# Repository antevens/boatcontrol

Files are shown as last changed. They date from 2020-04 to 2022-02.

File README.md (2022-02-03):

# Prototype, use at your own risk

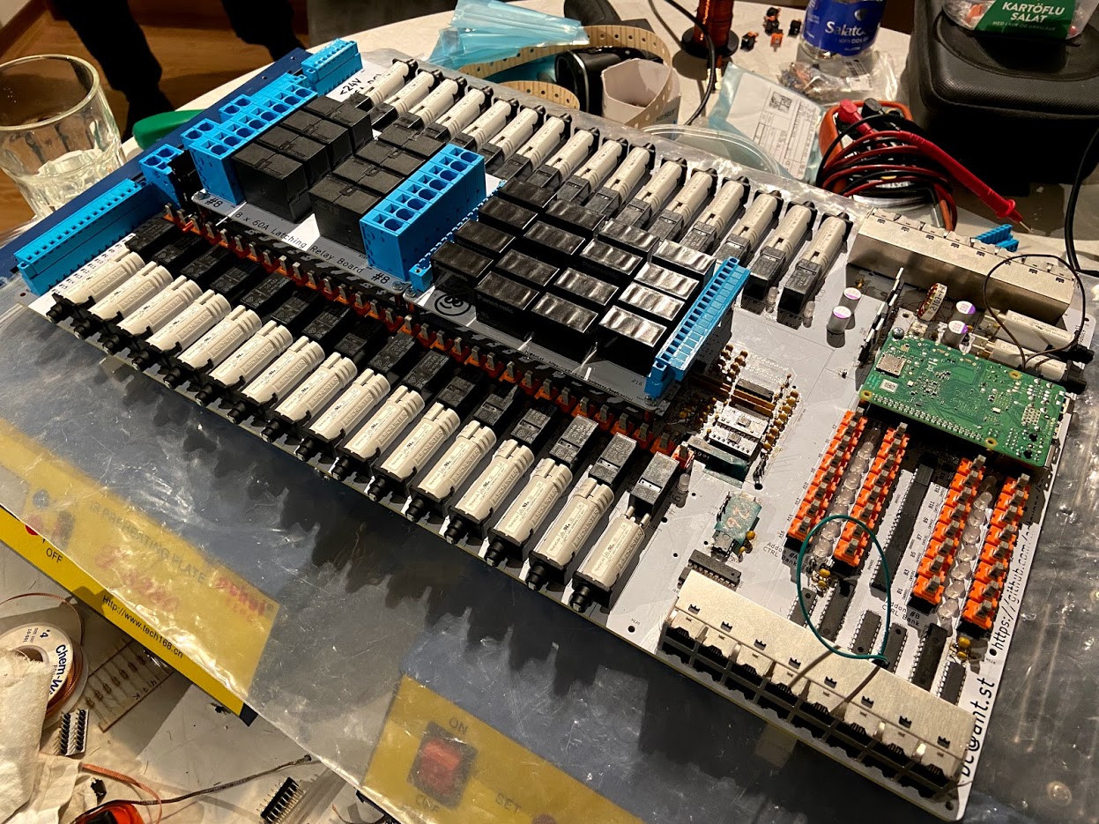
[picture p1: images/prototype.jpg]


# Boatcontrol

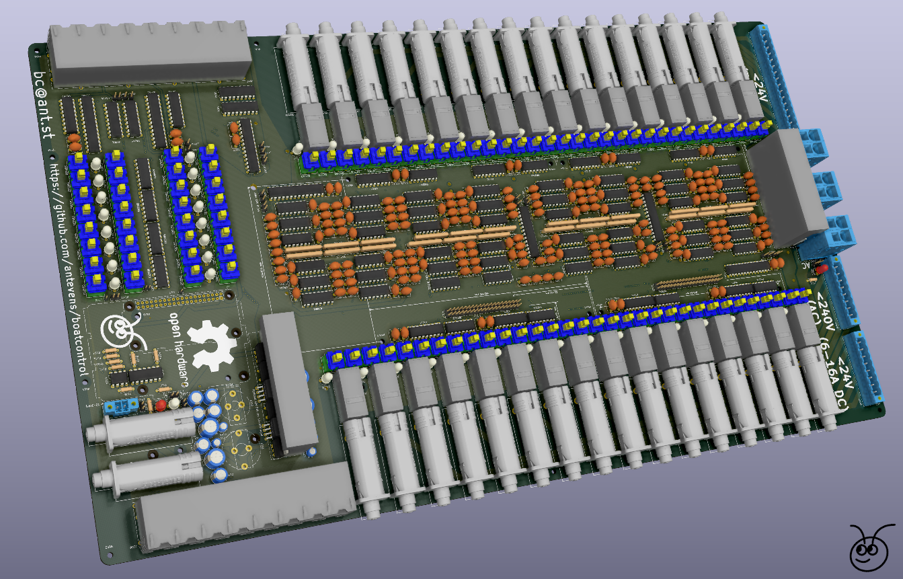
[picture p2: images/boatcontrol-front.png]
Boatcontrol Rendering_Front

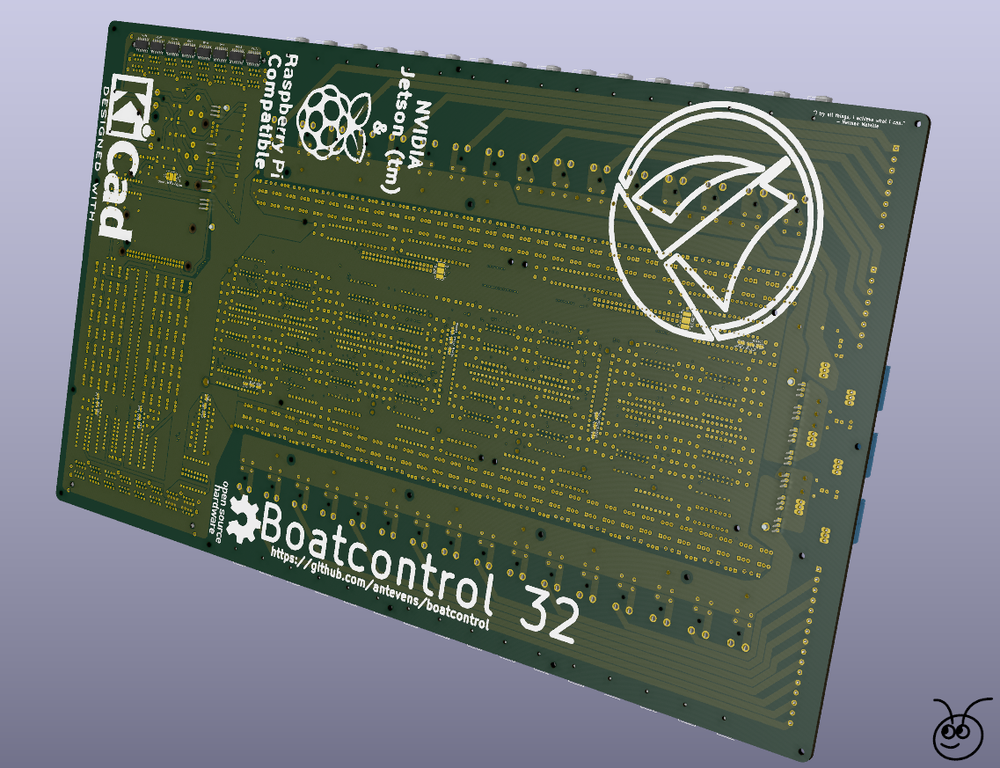
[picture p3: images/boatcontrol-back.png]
Boatcontrol Rendering_Front


## About

Boatcontrol is an open hardware design for a marine grade SMART/IoT electrical
distribution panel and electronics platform (boat) controller.

It's an I/O breakout board capable of switching 32 onboard laching relays and
optionally 32 momentary/laching relays using addon boards switchnig  up to 60A
AC/DC 0-400V per circuit.

The "smart" part is provided by either a **Raspberry Pi** HAT or a
**Nvidia Jetson** (Nano/Xavier NX) either of which can be mounted on the board.

All critical parts are designed to be field serviceable, components using
through-holes are used where possible for better durability in mobile marine
environment. Note that these boards need to carry significant amounts of current
and high voltage and as such PCB thickness and clearances are CRITICAL along
with proper thermal management.

Special care has been taken to limit idle power consumption wherever possible, on
it's own the board will only consume 15 Milliwatts when idle, if a Raspberry Pi (RPi) Zero is
mated it will add 80-120 Milliwatts, a fully fledged RPi 4 with all the bells and
whistles will add up to 3.4 Watts, a Jetson Xavier NX will bring the total to
10-15 Watts depending on configuration. Jumpers are provided where applicable
to disable LEDs to reduce power consumption when idle. Each active indicator LED
will likely consume 10-20 Milliwatts. Note that using a momentary add-on board can increase
the power consumption substancially depending on which relays are used and how
much time they spend on the "ON" position.

Effort was taken to make the boards as reliable as possible and enable them to
be operated in emergencies and under failure conditions. All circuits can be
operated manually on the board as long as the board has a power source over 6v
and below 30v (see optional 12V vs 24V operation and PSU).
Operation using external 5V TTL inputs via the RJ45 connectors is
available regardless of the state or presence of the RPi/Jetson.

The board can be set to run in either 12V or 24V mode, for operation
over 13V please make sure the optional 12V PSU components are in place and
the appropriate solder jumpers bridged.
For 12V operation make sure the 12V bypass jumper/solder pads are bridged.

## PCB Stack & Manufacturing

The design includes a main board and (at the time of launch) two optional addon
boards, the primary board is designed for 4 layer 2.4-3.2mm PCBs with the following sizes/layers:

#### Main board - 536mm x 308mm (just over 21" x 12")
* Front Power, 6oz (220um) copper, min spacing 0.500mm)
* First Signal, 1oz (35um) copper, min spacing 0.250mm)
* Second Signal, 1oz (35um) copper, min spacing 0.250mm)
* Back Power, 6oz (220um) copper, min spacing 0.500mm)

#### Addon boards - 153mm x 106mm (just over 5" x 4")
* The high current daughter board is designed for 4 layer 1/13oz (35/450um) copper.
* The non-latching daughter board is designed for 4 layer 1/6oz (35/200um) copper.
* The non-existent current sensing daughter board .. will probably use 6oz copper.
* The non-existent Full ESD optocoupler/isolator board .. will probably use 1oz copper.

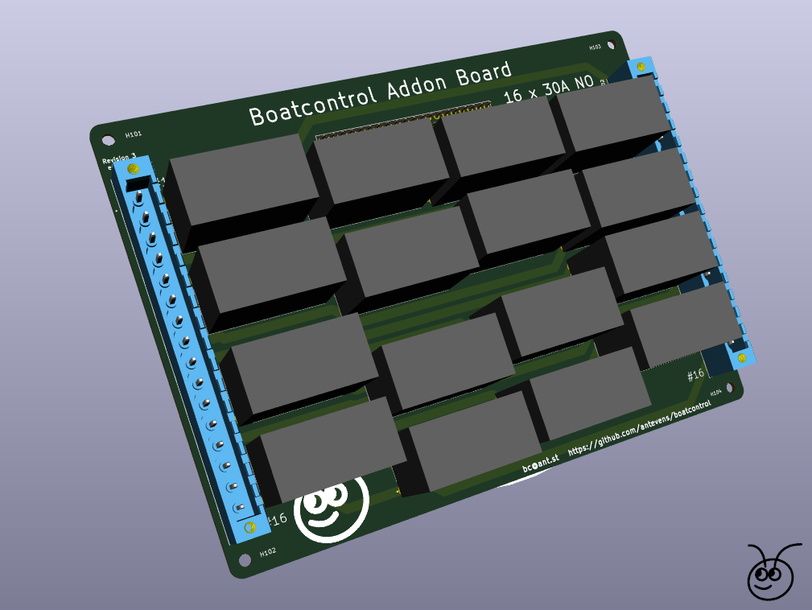
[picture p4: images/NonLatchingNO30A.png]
Boatcontrol Non Latching Relay Addon

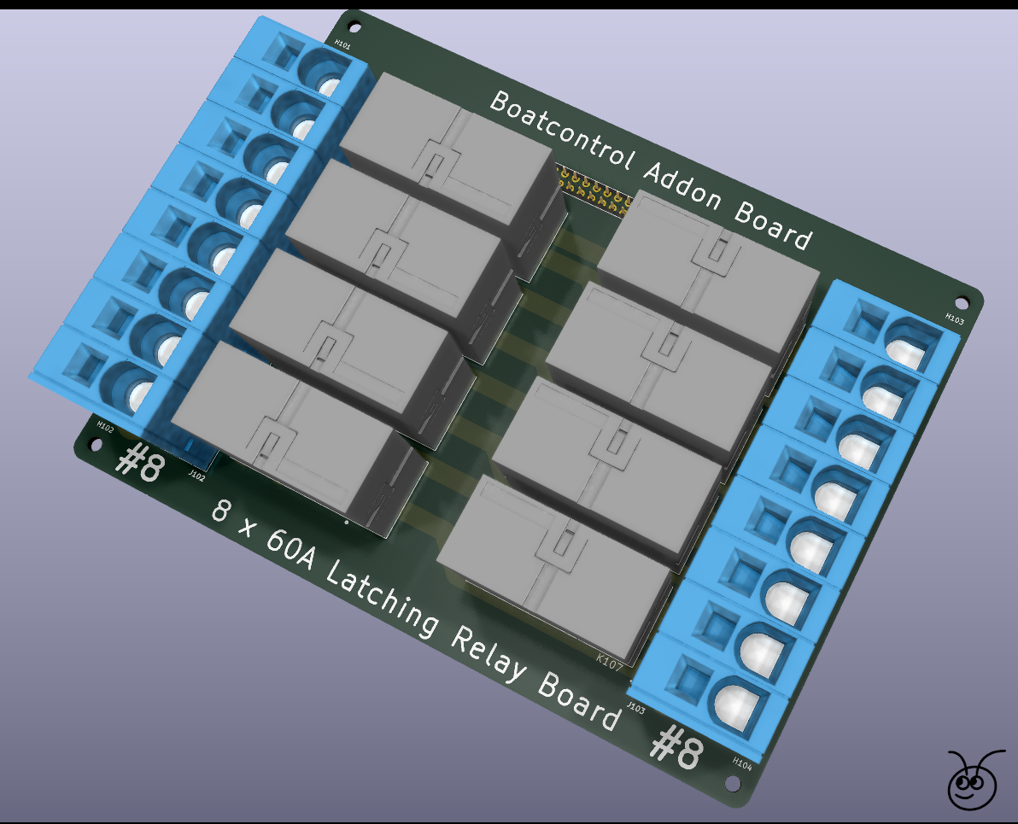
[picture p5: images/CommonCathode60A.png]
Boatcontrol Latching Relay Board


PCB Stack Thickness of daughter boards can vary as long as they are over 1mm

It's important that the power layers are on the outside for cooling purposes,
internal layers would require substantially thicker copper layers.

There aren't very many PCB manufacturers around that will/can produce a board
like this, especially in small quantities and the tooling fee will be a
substantial part of the total cost.

At the time of writing I would estimate at least $400 USD for tooling
setup and then $350 USD for each board manufactured. The manufacturers that
have online order forms for 4 layer heavy copper PCBs are:

* https://www.pcbcart.com
* https://www.pcbway.com
* https://pcbgogo.com

Note that these costs are only for the PCB, not for assembly or parts.

Note that a regular PCB panel is 457 x 610 (18" x 24"), each panel therefor can
acomidate 1 main board and 3 addon boards, consider this when ordering boards
and possibly create your own panel if your addon boards can use the same layer
stack as the primary board.

## Enclosure

Any reasonably sized enclosure will work but this board was designed to fit in
the **Fibox PC 5638 18T** (a custom mount plate will be needed since PCB standoffs don't
line up with the box attachment points).

This should give a rating of IP65/IK09

https://www.fibox.com/catalog/product/2393/2539557_ENG3.pdf

All cables should be installed with cable glands and drip loops, only install
cable glands on the bottom and optionally sides of the box, avoid making any
holes in the side facing up.

## Components, features and Bill of Materials

The components required to fully populate the board will typically cost around
{INSERT_BOM_COST}, here are full BOM carts from Mouser and DigiKey.

* {INSERT_LINK_TO_DIGIKEY}
* {INSERT_LINK_TO_MOUSER}

### Switches
Onboard switches can be momentary or locking depending on preference and application.
Typically one would use momentary switches for latching relays and locking
switches for non-latching relays.* For operating things like bilge pumps or
other devices that should only be turned on momentarily it might be beneficial
to use a non-latching relay with a momentary push button.

If for some reason locking switches are used with latching relays care must be
taken since most latching relay coils can't withstand being energized for long
periods and ideally should only be energized for less than a second*

The onboard switches are primarily for use in emergencies and debugging and while
they do provide protection against powering two coils in the same relay at the
same time they do not restrict the time a coil is energized unlike the RJ45 or
GPIO inputs.

All DPDT E3 series switches from Panasonic should work such as the ESB30 and ESB33
series, note that locking ESB30 switches can be converted to momentary
operation very easily even after soldering.

*The only exception to this would be if a user wants
to be able to physically disable a particular relay/circuit in which case two
locking relays can be used, if both of them are engaged at the same time they
will prevent all signals from reaching a latching relay behind them and at the
same time prevent each other from energizing the relay.

### Circuit breakers

The Schurter T9-818 breakers are  available in 3-15A current ratings and can
handle up to 48VDC and up to 240VAC.

The main board has a total of 32 breakers in 3 bank configurations, the board
can be outfitted with any configuration of breakers as long as the total does
not exceed 60A per bank or if a bank exceeds 60A then it should be protected by an
external 60A AC or DC breaker.

### The main (base) board layout includes sockets/circuits for:

#### 16 x 0-24V DC Common input channels/circuits:
* Input polarity protection and indicator LED
* Latching relay rated for 24V DC
* Thermally fused to 3A (can be swapped for 6A, 10A and 16A)
* Total current of these circuits should not exceed 60A

#### 8 x 0-24V DC Common input channels/circuits:
* Input polarity protection and indicator LED
* Latching relay rated for 24V DC
* 4 x thermally fused to 6A (can be swapped for 6A, 10A and 16A)
* 2 x thermally fused to 10A (can be swapped for 6A, 10A and 16A)
* 2 x thermally fused to 16A (can be swapped for 6A, 10A and 16A)
* Total current of these circuits should not exceed 60A

#### 8 x 100-250V AC Common input channels/circuits:
* AC Live/Neutral indicator LED
* Latching relay rated for 24V DC
* 4 x thermally fused to 6A (can be swapped for 6A, 10A and 16A)
* 2 x thermally fused to 10A (can be swapped for 6A, 10A and 16A)
* 2 x thermally fused to 16A (can be swapped for 6A, 10A and 16A)
* Total current of these circuits should not exceed 60A

## Addon boards
Addon boards connect to the main board using a 2 x 20 female pin header.
The main board male connectors are reversed compared to the GPIO header to avoid
confusion and prevent RPis or Jetson boards from being accidentally connected to
an addon-board header.

### Latching Relay Addon Board:
* 8 x 0-277V AC/DC Individual input/output channels/circuits
* Individual channel current should not exceed 60A
* No circuit breakers, polarity indicators or protection

### Momentary (Non Latching) Paired Addon Board:
* 16 (8 pairs*) x 12V DC non latching input/output channels/circuits
* Individual channel current should not exceed 32A
* No circuit breakers, polarity indicators or protection

_Non-latching Relays are paired and only one of a pair can be powered at any given time._

_All relays on a board share a common "Anode"/"Cathode", make sure to
adjust the solder-jumpers on the backside for the type of relays used so that
the relay polarity is correct. and that the correct driver array is chosen
(ULN2803A vs. TBD62783APG)_

Keep in mind that there is no requirement to fully populate the board and a partially
populated board is a great way to plan for future expansions given that the
board is field serviceable assuming the heavy copper soldering is done.

## Modes of operation
Each channel/circuit can be controlled using three different methods:

1. Using the onboard switches (these directly energize the relay coils)

2. Using two external switch signals wired up using CAT5/6 with RJ45
connectors. The signals use 5V TTL logic and are active HIGH.
The signals are filtered for noise and duration to protect the relays,
this ensures that only one coil can be energized at any given time and
only for a period of 1 second. Due to this filtering these can be safely
wired to 3-way "Latching" wall/panel switches or momentary push buttons.

3. Using I2C via the 2x20 Header, typically this would be done using a
Raspberry Pi (RPi) or Nvidia Jetson, for power efficiency consider using a RPi Zero.
See Node-Red source for IoT web based interfaces that can run on these platforms.

* Onboard bi-colour LEDs indicate coil energy state and pulses to "ON"/"OFF" coils.
* For latching relays RED indicates the circuit being turned ON while GREEN indicates the circuit being turned OFF.
* For non-latching relays RED and GREEN each represent a separate relay in a pair.

## Technical details

While the scale is disproportionate the main board is really just a rather large
Raspberry Pi HAT though it does not require an RPi to operate.
__Note that the board will act as a power supply for the RPi and Jetson
Nano eliminating the need for a separate PSU.__
__The Nvidia JetsonXavier products such as the NX and AGX will still need a separate (19V)
power source.__

All communication between the RPi and the board is done using I2C, this only
requires 2 pins/wires and makes it safe to use in combination with most if not all
other HATs. In particular it can co-exist with AIS and GPS hats like the dAISy though you
might want to run your chart-plotting or navigation software on a separate
RPi/Jetson NX and have a dedicated micro-computer for controlling your electrical system.

The Sailor Hat or PICAN-M HATs might be of particular interest to allow the
Boatcontrol board to act as an NMEA 0183/2000 or Seatalk device.

* https://hatlabs.fi/product-category/sh-rpi/sh-rpi-devices
* https://www.skpang.co.uk/collections/hats/products/pican-m-with-can-bus-micro-c-and-rs422-connector-3a-smps
* https://copperhilltech.com/pican-m-nmea-0183-nmea-2000-hat-for-raspberry-pi/

### RJ45 Connectors & Remote I/O
The top/right (J108) RJ45 connector is used to remotely control relays on the main
board. Each RJ45 socket controls 2 latching relays or 2 non-latching relay pairs (4).
Every socket consists of 4 separate 5V supply pins supplied via a 10KΩ resistor.

All J108 (top connector)inputs are ESD protected using clamp diodes in the
74HCT86 packs to the following standards:
* HBM JESD22-A114F exceeds 2000 V
* MM JESD22-A115-A exceeds 200 V

For long cable runs the resistor banks on the back can be replaced with lower
resistance values.

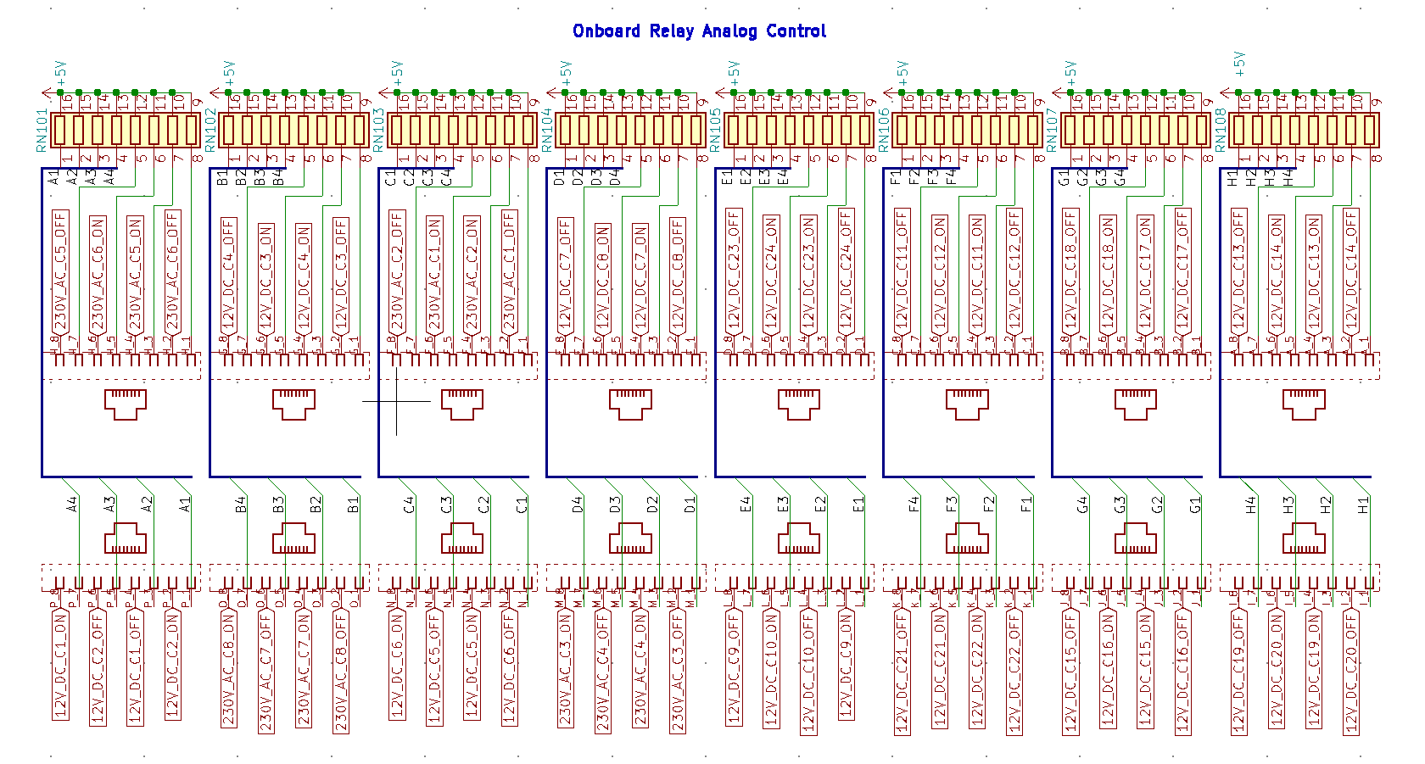
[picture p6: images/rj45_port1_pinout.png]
RJ45 Port 1 pinout


Half of the bottom/left (J107) RJ45 connector is used to remotely control addon
boards.

Each RJ45 socket can control 4 channels, typically controlling 2 latching relays
or 2 non-latching relay pairs (4).

**Note that for these connectors there are no current limiting resistors so
current is only limited by what the onboard PSU can supply and shorting this
can de-power the RPi/Jetson!**

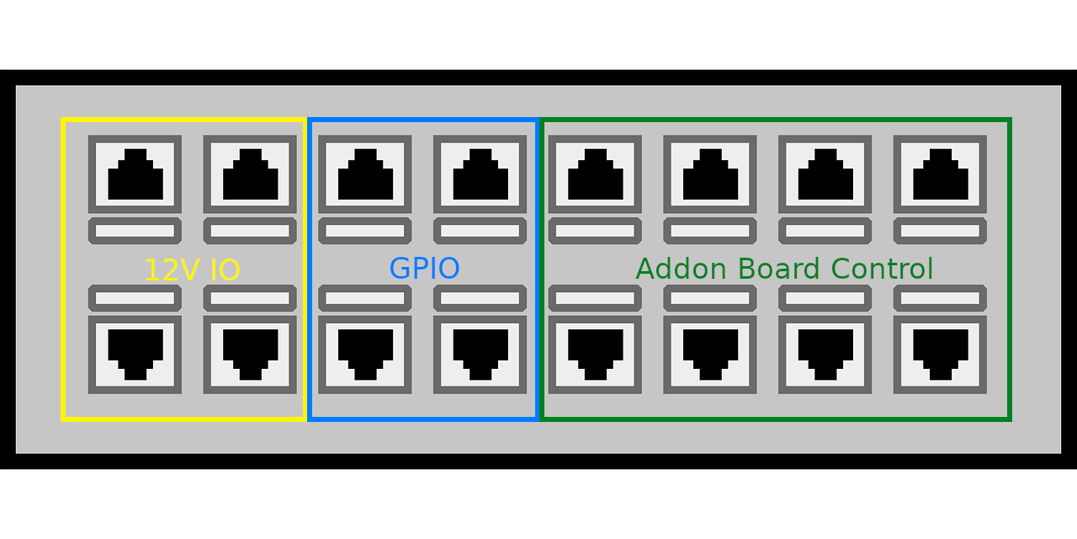
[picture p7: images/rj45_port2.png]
RJ45 Port 2 pinout

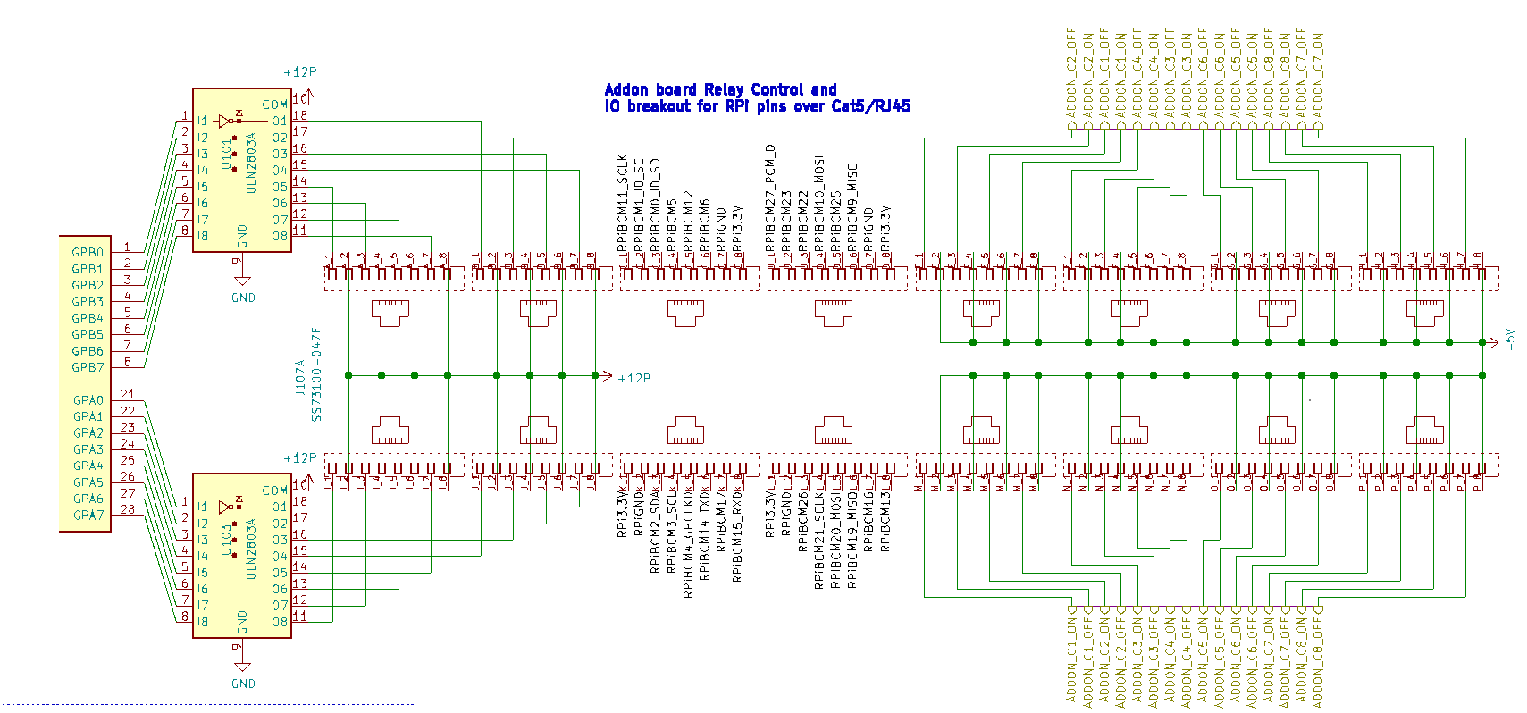
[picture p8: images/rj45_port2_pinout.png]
RJ45 Port 2 pinout


**Pairing is important for all RJ45CAT5/6 wiring, it's highly
recommended that the source/sink to control each relay uses a twisted pair,
this will minimize loss and interference. Pairs are typically colored as shown here**

Cat5/6 Twisted pairs

_Advanced uses may also include shielding but this is beyond the scope of this document._

#### 12V "High Voltage/Current" Pins
There are 16 extra IO pins that can provide up to 500mA each, this is provided
using an MCP23017 and a ULN2803* with a clamp diode. Examples of use cases would
be external relays, solenoids, small motors, high power LEDs, Cameras, etc.

_*can be substituted with a TBD62783APG to swap polarity from 12V source to GND
sink._

#### Raspberry Pi / Jetson  I/O
All pins from the GPIO header are made available via RJ45 to allow easy
expansion and remote mounting of devices such as GPS and AIS devices.

_Note that the 5V pins are shared with the RPi and maximum currents governed by
the RPi design not the Boatcontrol._

*_Note that no additional protection or filtering is provided, the pins are
simply mapped from the RPi GPIO header directly to RJ45 without any provision
to minimize signal degradation or distortion._

_Note that this includes the I2C bus which can be used to communicate directly
with all devices on the main and addon boards_

**IMPORTANT** - Since no extra ESD filtering or opto-isolaion is provided for
thes GPIO ports if there there is any chance of surges or high voltages these
should be isolated from the board using digital isolators or optocouplers
and transient voltage suppressors. For remote installations of the
Raspberry Pi/Jetson you might also want to add debounce and provide 3v from an
isolated source.

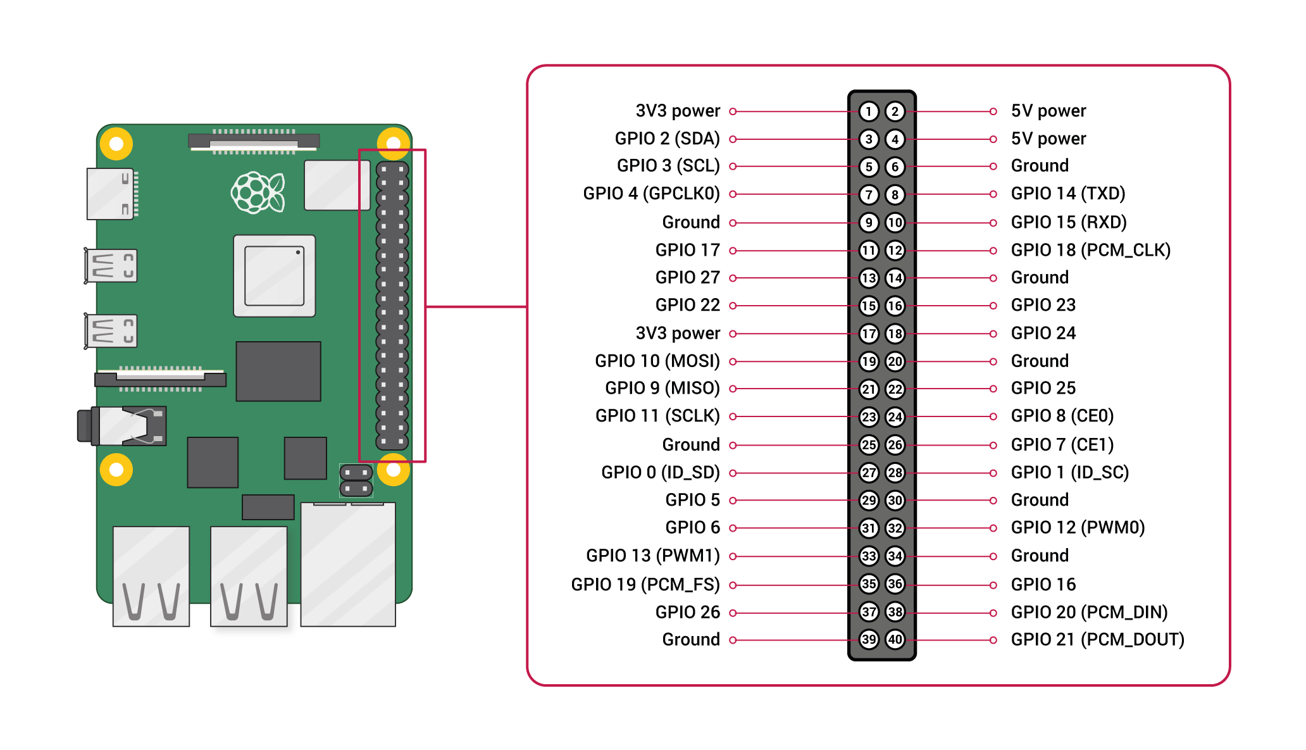
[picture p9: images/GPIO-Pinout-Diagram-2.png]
Raspberry_Pi_Pinout


### RPi HAT / Jetson GPIO Interface
Using the GPIO header there are two ways to connect an RPi or Nvidia Jetson
device to the board.
1. Install female pin header on the Boatcontrol, mount the device directly in
the upside down position, if you choose this option make sure the particular board you are mounting has
enough clearance.*
2. Install a male pin header on the Boatcontrol, mount the device using a
   ribbon cable.

*While the RPi Zero is guaranteed to fit and with long headers all the
Pi/Pi2/Pi2/Pi4s should fit you should make sure your device fits before
choosing this mounting method.

_If using a Jetson Xavier NX or AGX make sure you use the horizontal inductors for the
PSU since the vertical arrangement can block one of the mounting holes._

### Addon cards
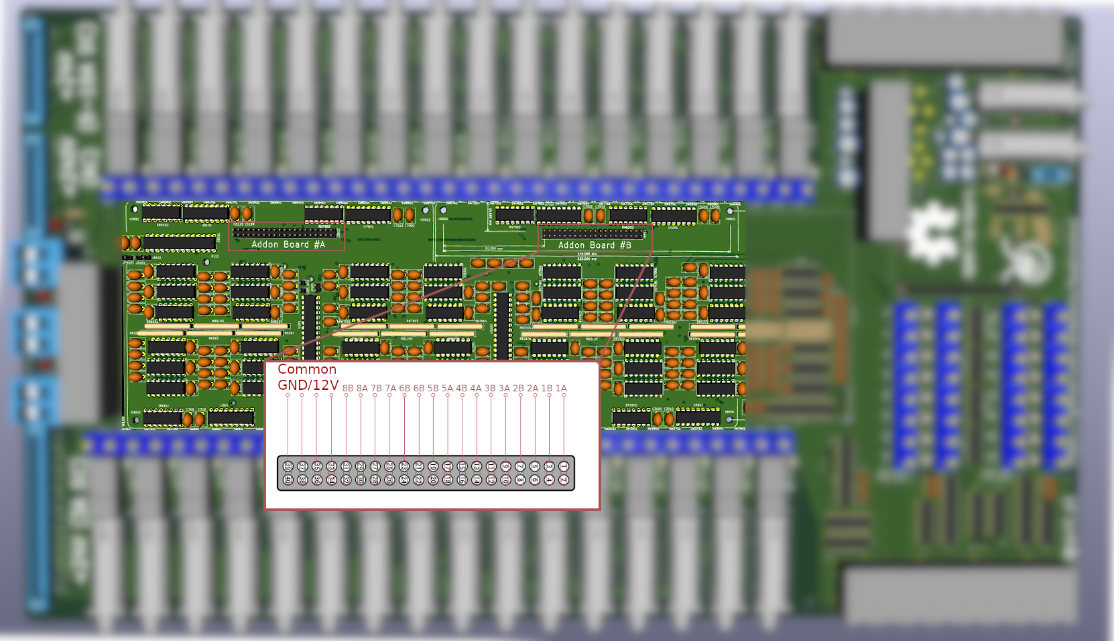
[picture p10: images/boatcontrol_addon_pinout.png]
RJ45 Port 2 pinout


### I2C interface and addresses
The I2C addresses of the IO Expanders can be modified* using solder jumpers on
the backside of the PCB but the defaults are:

    0x20 (32) 3A Common Input DC #1-8
    0x21 (33) 3A Common Input DC #9-16
    0x22 (34) 6/10/16A Common Input DC
    0x23 (35) 6/10/16A Common Input AC
    0x24 (36) 60A Individual AC/DC
    0x25 (37) Additional IO #1 to RJ45 Cat5/6
    0x26 (38) Additional IO #2 to RJ45 Cat5/6

*Bring plenty of watts, it's a 6oz PCB!

# Software
One of the primary advantages of having the GPIO interface and using a
Raspberry Pi or Nvidia Jetson to interface with the board is the simplicity and
ease of use allowing each installation to be customized for the particular boat
and users, changes can be made in real-time using a web browser and all the
functionality and features are accessible from any web enabled device onboard
or remote.

The following are screenshots from development UIs used to debug and test the
hardware, they show some of the functionality that's possible including
day/night views, automated alerts and functionality.

This particular interface is built using Node-Red and is running on an RPi 4.
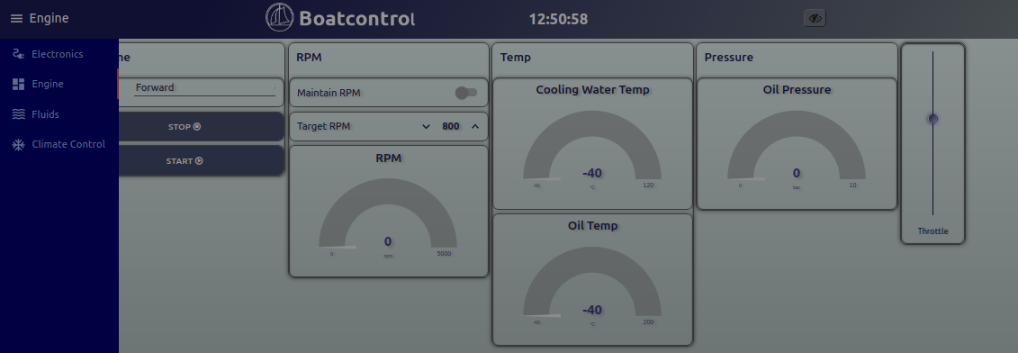
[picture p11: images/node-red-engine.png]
Node-Red Engine

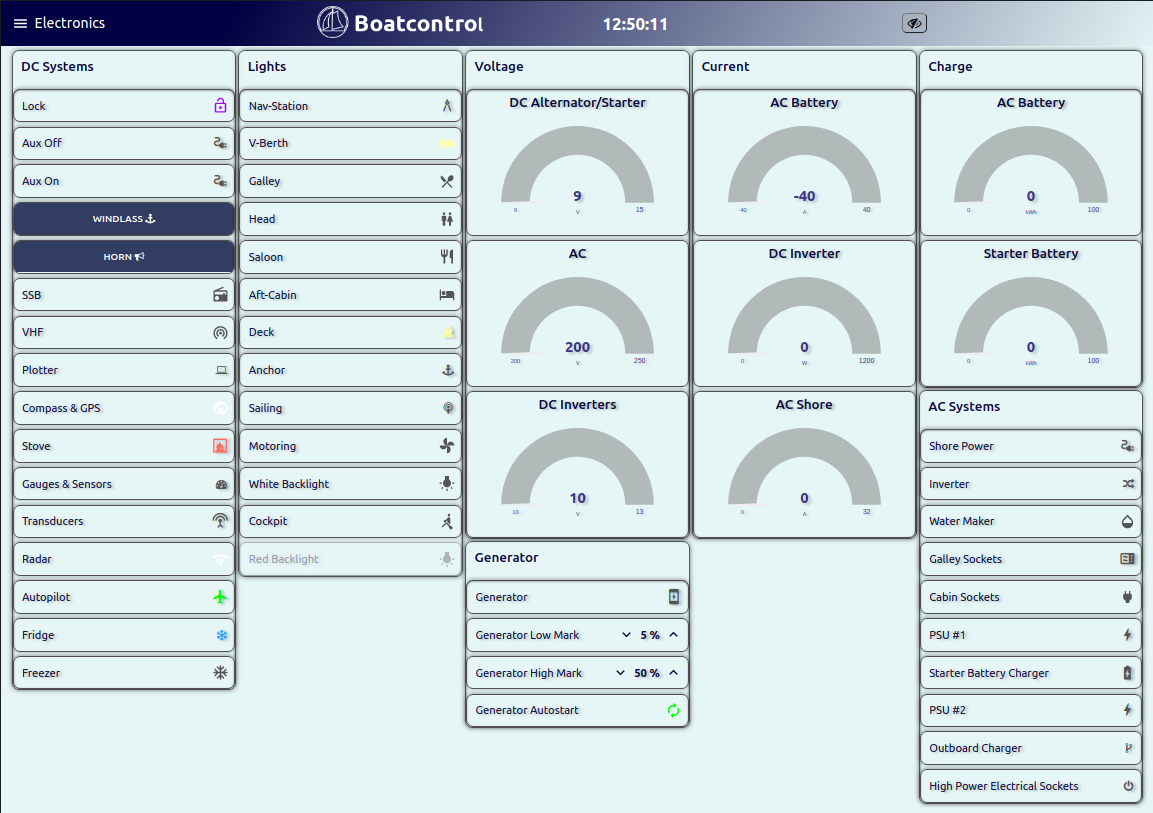
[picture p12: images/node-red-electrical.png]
Node-Red Electrical

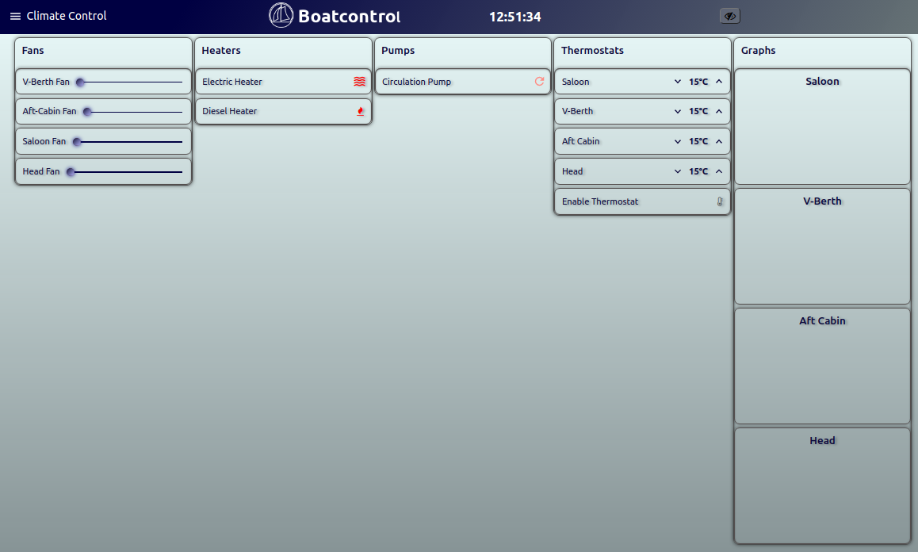
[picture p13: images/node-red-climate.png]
Node-Red Climate

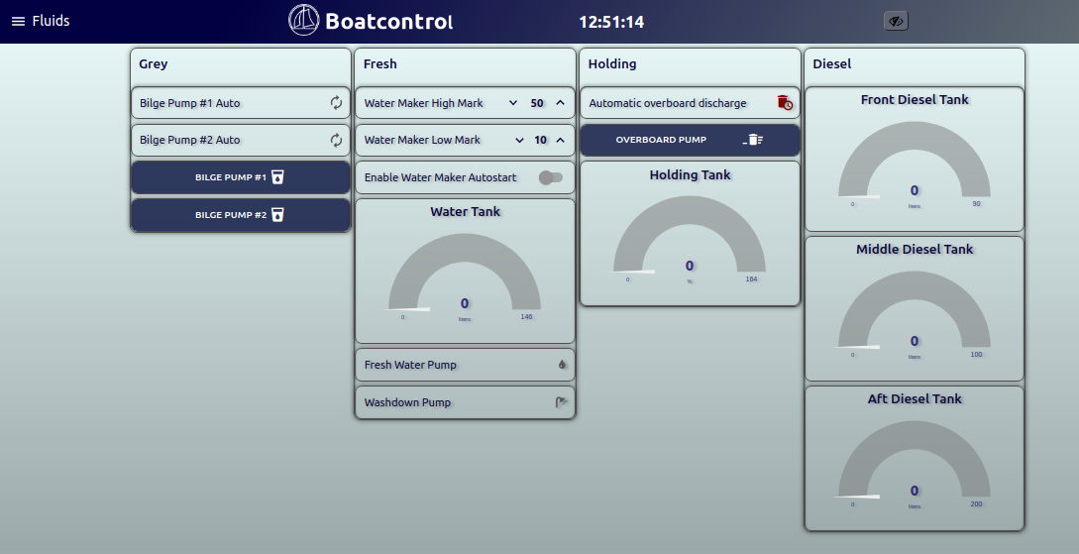
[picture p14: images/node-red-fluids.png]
Node-Red Fluids

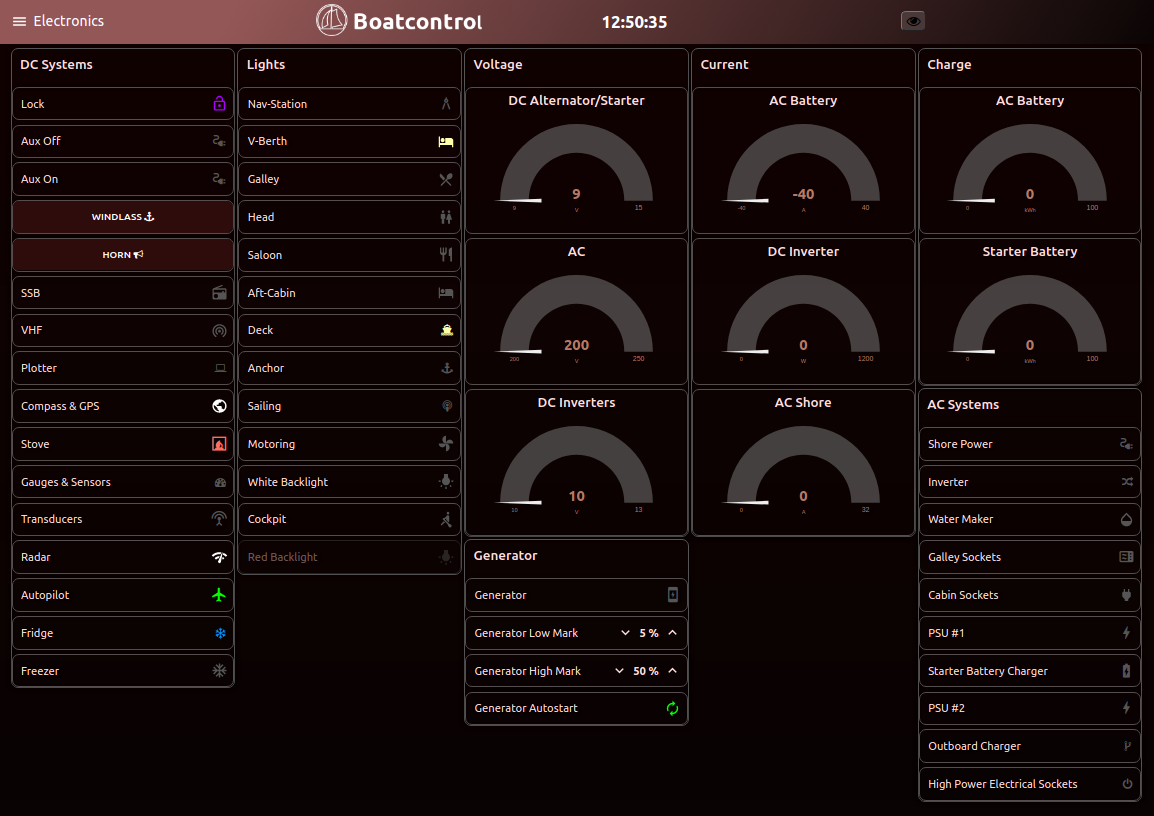
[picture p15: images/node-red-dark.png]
Node-Red Fluids


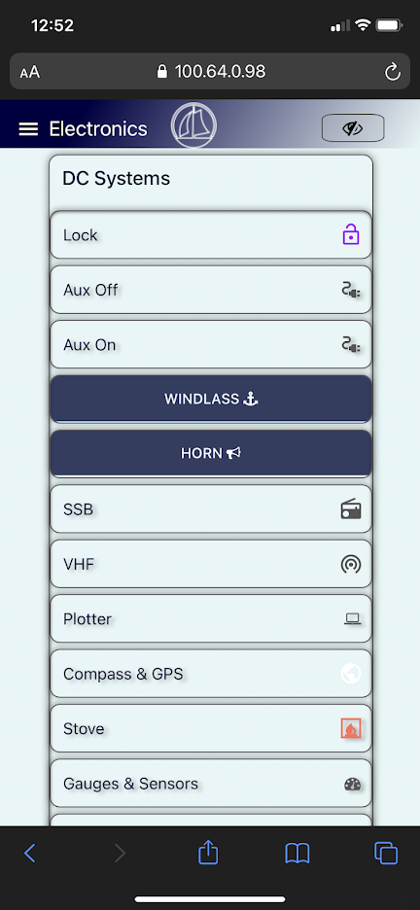
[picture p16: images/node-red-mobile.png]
Node-Red Mobile Interface


# Open Hardware

Feel free to modify this to suit your own needs or have it made as it's
currently configured. Be careful when upgrading circuit breakers to not exceed the
current/thermal capacity of the board. If you use thinner copper than 6oz make
sure to appropriately downgrade the thermal breakers to reduce maximum current.

## Bus bars, jumper wires and 2 layer boards

Depending on where you live and your requirements it might make more sense
for you to use laser cut copper bus bars or solder wires on the back of your PCB to
avoid the expensive 6oz copper layers.

The PCB was architected to facilitate 1oz / 2 layer construction, there is a
git branch called [2layer](../../tree/2layers) which is the last version supporting 2 layers. *In
theory* this could be made with 1oz copper and used with bus bars or jumper
wires but it's not been kept up to date. Let me know if you want to use this
and we can probably work together to merge relevant changes.

## Key design decisions and parameters

* All critical components are through-hole for field maintenance on moving platforms and secure attachment for vibration and G loads.
* All relays can be controlled from either the RPi/Nvidia or using analog control signals via RJ45/CAT5/6 connectors/cables.
* All onboard relays are latching dual coil with individual control circuits.
* All analog input channels have pulse generators for the relays to protect them from overheating.
* Built-in high efficiency 5/12v step down converters to power the RPi/Nano and logic components and supply current for analog control.
* 8x 3-16A 250V AC shared bus protected circuits
* 24x 3-16A 12-24V DC shared bus protected circuits
* 32x 12-24V 500mA DC Logic/Relay breakout via RJ45
* Optional 16x 250V AC non-latching unprotected add-on board
* Optional 8x 60A 277V AC latching individual unprotected add-on board
* All onboard DC channels are polarity protected with high efficiency PFETs
* Protection is provided using thermal circuit breakers, the permitted amperage can be changed by switching out breakers, no breakers are provided for the 60A circuits, suggest using external breakers.

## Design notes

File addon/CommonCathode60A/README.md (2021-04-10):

Addon board for Boatcontrol 32.

The Boatcontrol 32 is a smart distribution panel and electrical system for on/off-grid and hybrid backup power systems that need to handle 12-24v DC 110-115v AC and 200-250V AC systems.
A perfect companion to a SMA Sunny Island or Sunny Boy Storage, Fronius or other battery inverters.

It's a one stop PCB that allows a Raspberry Pi (RPi) or Nvidia Jetson to control your entire electrical system while retaining full analog control from external switches and allowing manual override onboard in case of emergencies.
This addon board adds 8 x 60 AC/DC relays.
https://github.com/antevens/boatcontrol/tree/master/addon/CommonCathode60A

BoatControl
https://github.com/antevens/boatcontrol

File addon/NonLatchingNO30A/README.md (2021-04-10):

Addon board for Boatcontrol 32.

The Boatcontrol 32 is a smart distribution panel and electrical system for on/off-grid and hybrid backup power systems that need to handle 12-24v DC 110-115v AC and 200-250V AC systems.
A perfect companion to a SMA Sunny Island or Sunny Boy Storage, Fronius or other battery inverters.

It's a one stop PCB that allows a Raspberry Pi (RPi) or Nvidia Jetson to control your entire electrical system while retaining full analog control from external switches and allowing manual override onboard in case of emergencies.
This addon board adds 16 x 30A AC/DC relays.

Note that the relays are paired for manual override. When operating relayes in
emergency mode only one out of a pair can be operated at a time.

https://github.com/antevens/boatcontrol/tree/master/addon/CommonCathode30A

BoatControl
https://github.com/antevens/boatcontrol

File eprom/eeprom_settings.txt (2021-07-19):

########################################################################
# EEPROM settings text file
#
# Edit this file for your particular board and run through eepmake tool,
# then use eepflash tool to write to attached HAT ID EEPROM 
#
# Tools available:
#  eepmake   Parses EEPROM text file and creates binary .eep file
#  eepdump   Dumps a binary .eep file as human readable text (for debug)
#  eepflash  Write or read .eep binary image to/from HAT EEPROM
#
########################################################################

########################################################################
# Vendor info

# 128 bit UUID. If left at zero eepmake tool will auto-generate
# RFC 4122 compliant UUID
product_uuid 13373550-1337-3550-0553-133770015337

# 16 bit product id
product_id 0x7001

# 16 bit product version
product_ver 0x000A

# ASCII vendor string  (max 255 characters)
vendor "Boatcontrol"

# ASCII product string (max 255 characters)
product "Boatcontrol 32"

# Custom binary data
custom_data
da7001
end

########################################################################
# GPIO bank settings, set to nonzero to change from the default.
# NOTE these setting can only be set per BANK, uncommenting any of
# these will force the bank to use the custom setting.

# drive strength, 0=default, 1-8=2,4,6,8,10,12,14,16mA, 9-15=reserved
gpio_drive 0

# 0=default, 1=slew rate limiting, 2=no slew limiting, 3=reserved
gpio_slew 0

# 0=default, 1=hysteresis disabled, 2=hysteresis enabled, 3=reserved
gpio_hysteresis 0

# If board back-powers Pi via 5V GPIO header pins:
# 0 = board does not back-power
# 1 = board back-powers and can supply the Pi with a minimum of 1.3A
# 2 = board back-powers and can supply the Pi with a minimum of 2A
# 3 = reserved
# If back_power=2 then USB high current mode will be automatically 
# enabled on the Pi
back_power 2

########################################################################
# GPIO pins, uncomment for GPIOs used on board
# Options for FUNCTION: INPUT, OUTPUT, ALT0-ALT5
# Options for PULL: DEFAULT, UP, DOWN, NONE
# NB GPIO0 and GPIO1 are reserved for ID EEPROM so cannot be set

#         GPIO  FUNCTION  PULL
#         ----  --------  ----
setgpio  2     INPUT     DEFAULT
setgpio  3     OUTPUT    DEFAULT
#setgpio  4     INPUT     DEFAULT
#setgpio  5     INPUT     DEFAULT
#setgpio  6     INPUT     DEFAULT
#setgpio  7     INPUT     DEFAULT
#setgpio  8     INPUT     DEFAULT
#setgpio  9     INPUT     DEFAULT
#setgpio  10    INPUT     DEFAULT
#setgpio  11    INPUT     DEFAULT
#setgpio  12    INPUT     DEFAULT
#setgpio  13    INPUT     DEFAULT
#setgpio  14    INPUT     DEFAULT
#setgpio  15    INPUT     DEFAULT
#setgpio  16    INPUT     DEFAULT
#setgpio  17    INPUT     DEFAULT
#setgpio  18    INPUT     DEFAULT
#setgpio  19    INPUT     DEFAULT
#setgpio  20    INPUT     DEFAULT
#setgpio  21    INPUT     DEFAULT
#setgpio  22    INPUT     DEFAULT
#setgpio  23    INPUT     DEFAULT
#setgpio  24    INPUT     DEFAULT
#setgpio  25    INPUT     DEFAULT
#setgpio  26    INPUT     DEFAULT
#setgpio  27    INPUT     DEFAULT

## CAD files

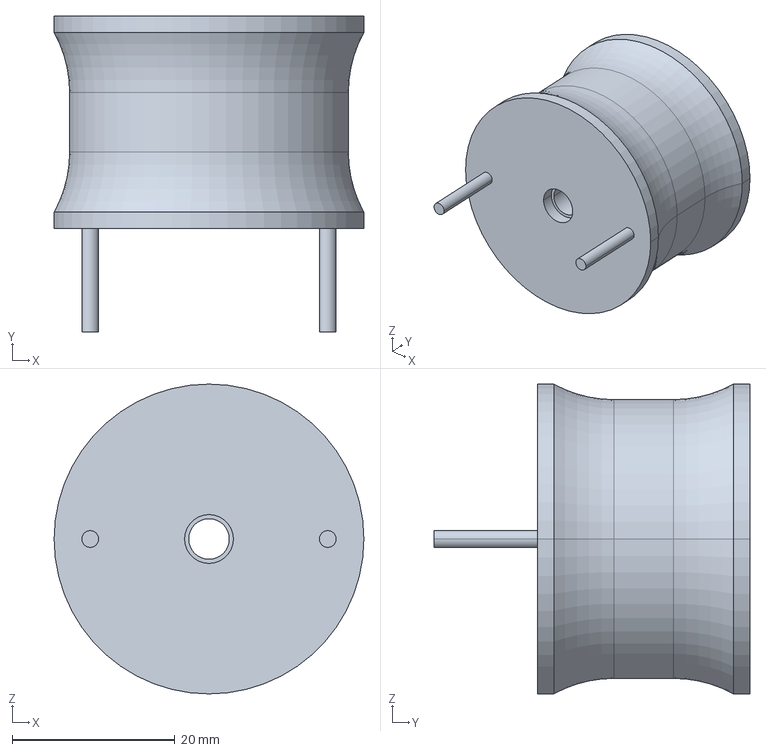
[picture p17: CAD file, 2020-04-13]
boatcontrol/1140-220K-RC/1140-220k-rc.stp
38.1 x 38.9 x 38.1 mm

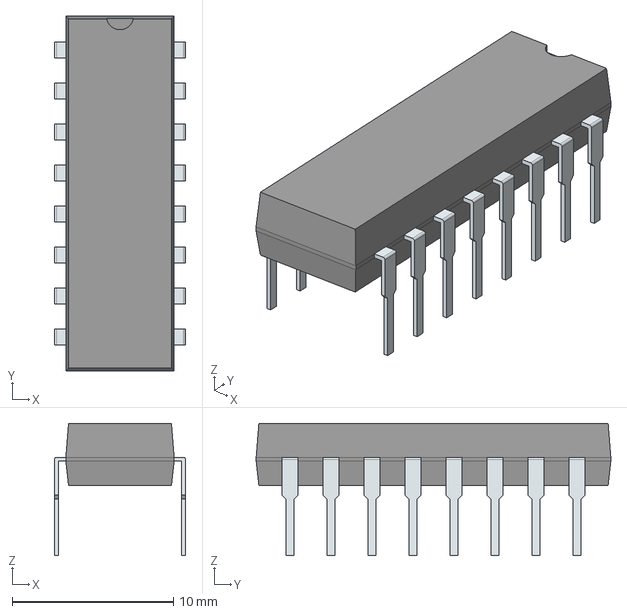
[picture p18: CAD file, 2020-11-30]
boatcontrol/4116R-1-103LF/4116R-1-103LF.stp
8.11 x 22.0 x 8.19 mm
PinsArrayLR

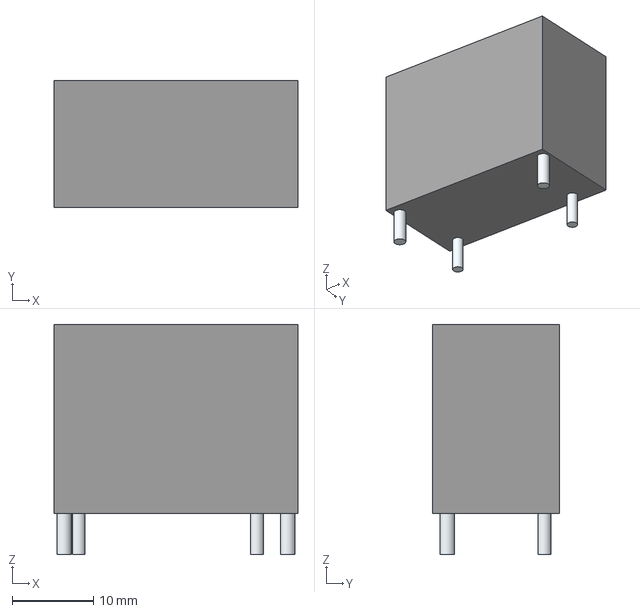
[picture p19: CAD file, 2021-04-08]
boatcontrol/ALFG2PF12/ALFG2PF121.stp
30.1 x 15.7 x 28.4 mm
Leads x 4

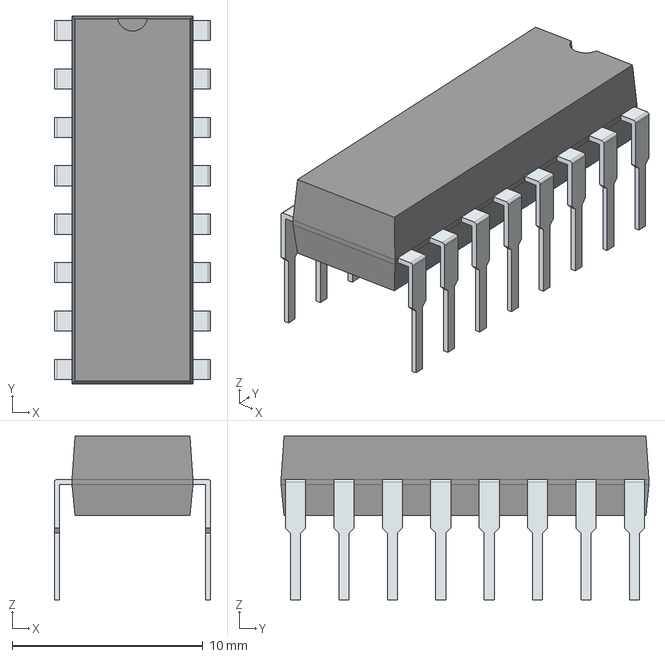
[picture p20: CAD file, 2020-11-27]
boatcontrol/CD74HCT221E/CD74HCT221E.stp
8.21 x 19.3 x 8.58 mm
PinsArrayLR

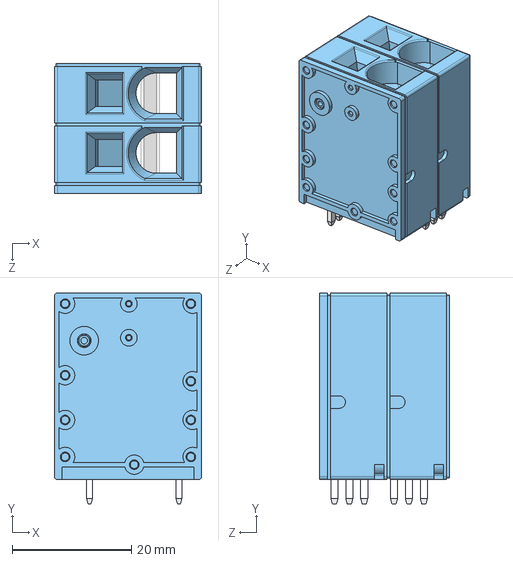
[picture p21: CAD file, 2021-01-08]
boatcontrol/CUI_DEVICES_TBL008-1000-02BE/CUI_DEVICES_TBL008V-1000-02BE.step
24.7 x 35.4 x 21.8 mm

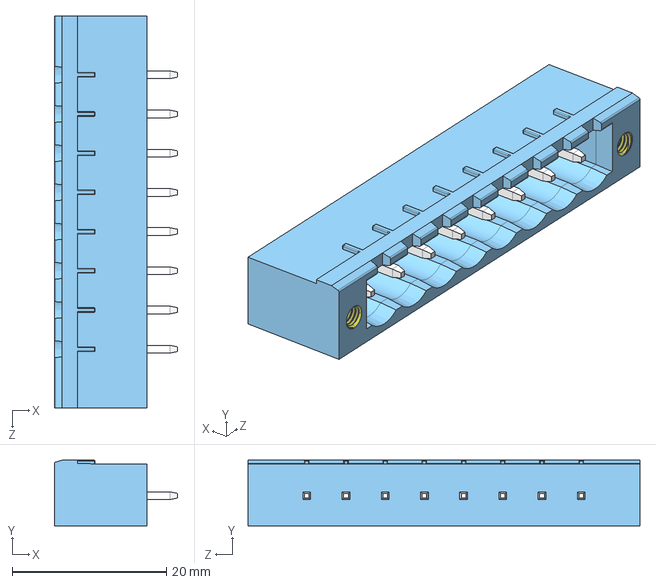
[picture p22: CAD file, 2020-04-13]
boatcontrol/CUI_DEVICES_TBP01R2W-508-08BE/CUI_DEVICES_TBP01R2W-508-08BE.step
16.0 x 8.50 x 50.8 mm

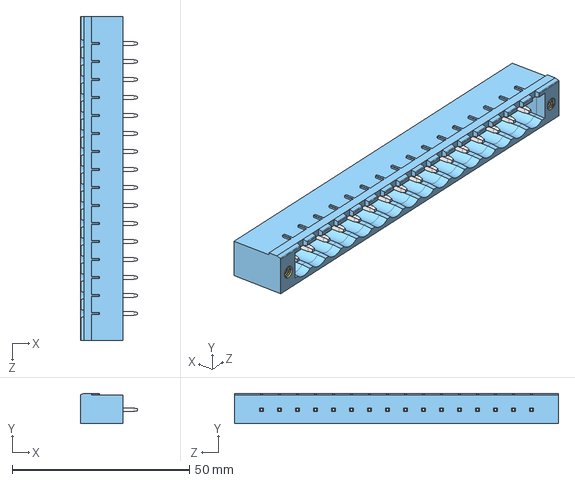
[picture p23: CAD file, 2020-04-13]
boatcontrol/CUI_DEVICES_TBP01R2W-508-16BE/CUI_DEVICES_TBP01R2W-508-16BE.step
16.0 x 8.50 x 91.4 mm

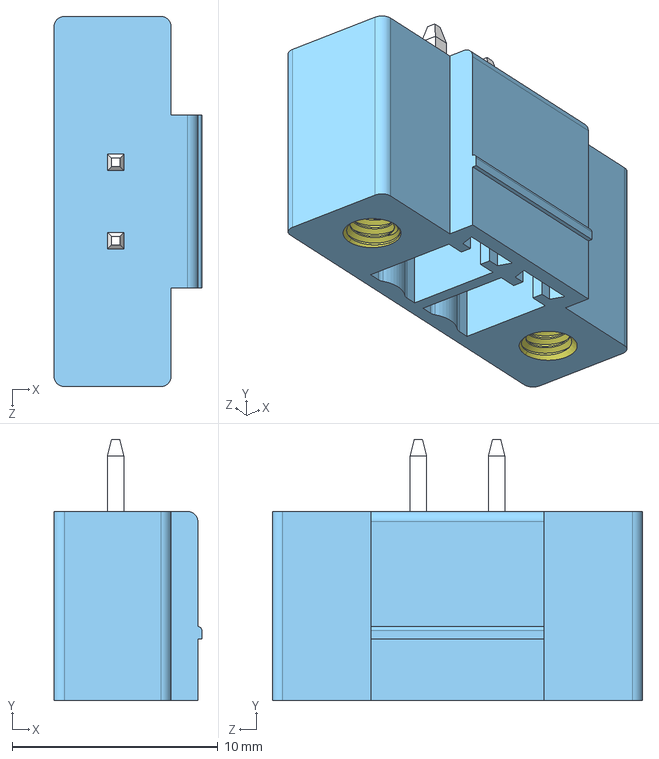
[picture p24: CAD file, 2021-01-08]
boatcontrol/CUI_DEVICES_TBP02R2W-381-02BE/CUI_DEVICES_TBP02R2W-381-02BE.step
7.20 x 12.7 x 18.0 mm

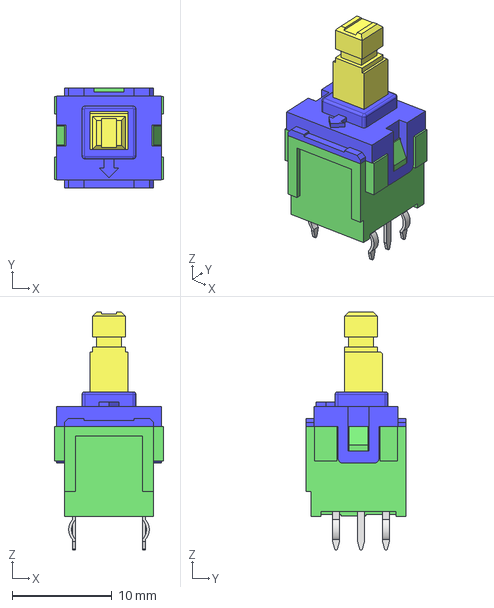
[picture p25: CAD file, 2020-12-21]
boatcontrol/ESB30B102/ESB30B102.step
10.9 x 10.0 x 23.9 mm

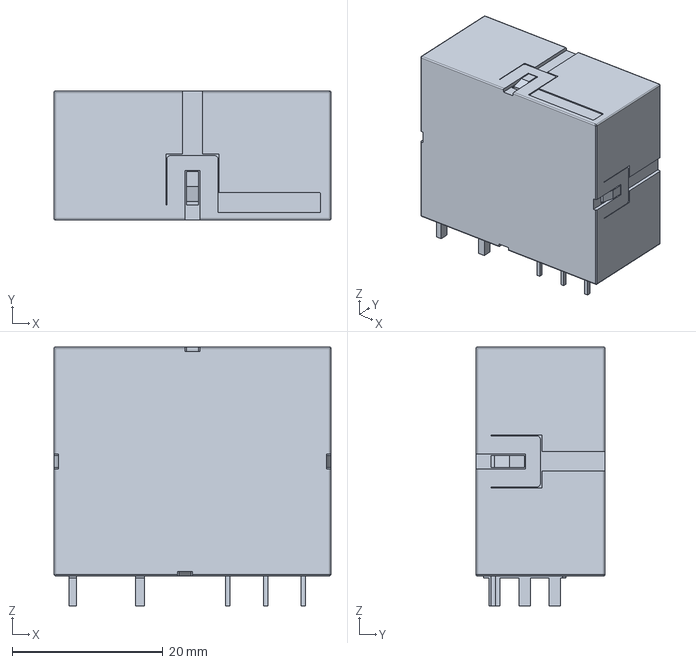
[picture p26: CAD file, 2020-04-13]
boatcontrol/EW60-1A3-CL12D04/c-2071366-2-b-3d.stp
36.8 x 17.2 x 34.4 mm

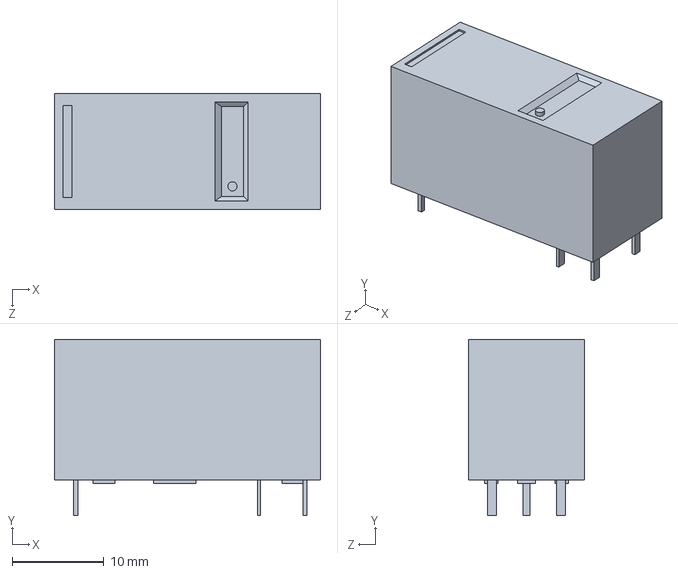
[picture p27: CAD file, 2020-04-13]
boatcontrol/G5RL_K1A_E_STEP/G5RL_K1A_E.step
29.0 x 19.2 x 12.7 mm

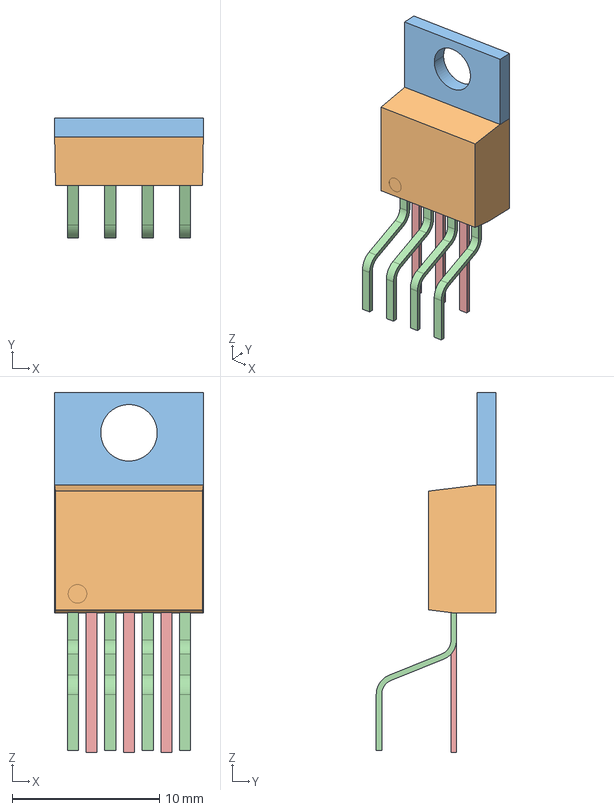
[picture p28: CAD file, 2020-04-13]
boatcontrol/LM2679T/LM2679T.stp
10.2 x 8.13 x 24.5 mm

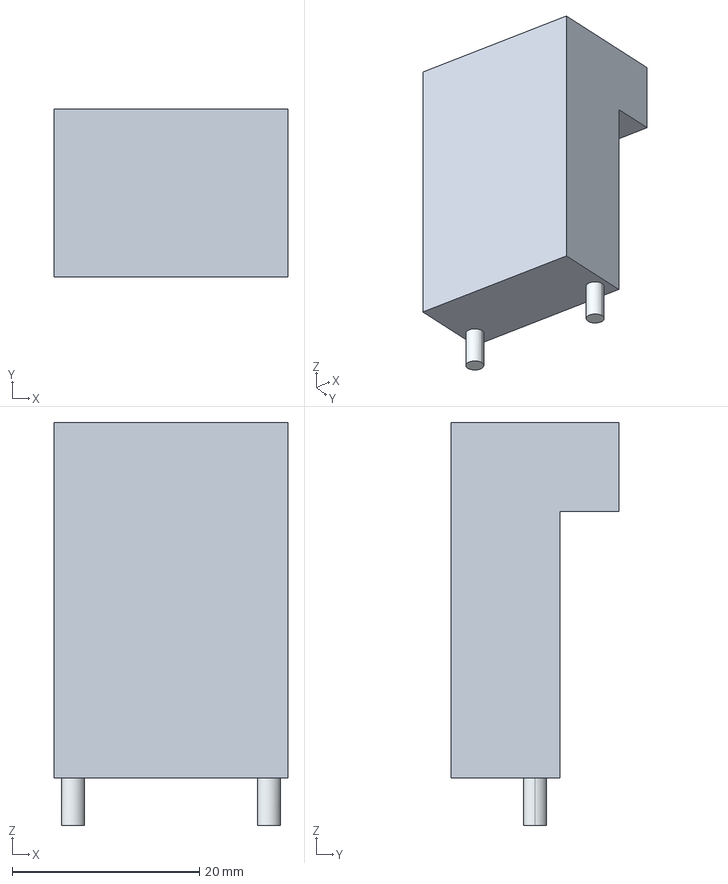
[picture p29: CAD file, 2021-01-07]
boatcontrol/OMNI-220-18-25-1C/OMNI-220-18-25-1C.stp
25.0 x 18.0 x 43.1 mm

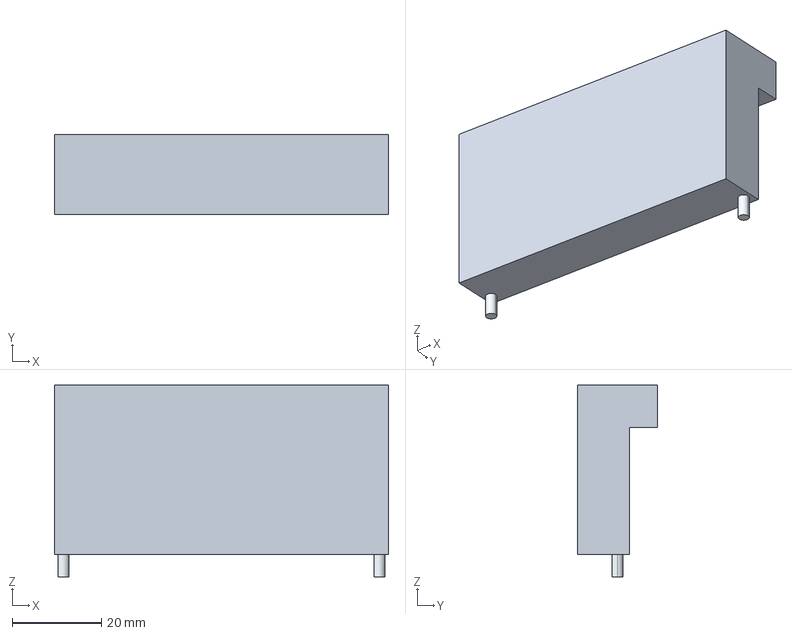
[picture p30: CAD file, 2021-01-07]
boatcontrol/OMNI-220-18-75-3C/OMNI-220-18-75-3C.stp
75.0 x 18.0 x 43.1 mm

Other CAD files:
boatcontrol/1140-680K-RC/1140-680k-rc.stp
boatcontrol/RaspberriPi4b/Raspberry_Pi_4B.step
boatcontrol/T9-818_step/T9-818.STEP
boatcontrol/TO-220-7/TO-220-7.STEP
boatcontrol/BELFUSE_SS73100047F/SS73100-047F.step
boatcontrol/CUI_DEVICES_TBL008-1000-02BE/CUI_DEVICES_TBL008-1000-02BE.step

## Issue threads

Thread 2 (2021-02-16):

Create non-latching relay board design

antevens, 2021-02-16:
Create a non latching relay board for controlling loads such as pumps and windlasses

antevens, 2021-04-14:
done

Closed 2021-04-14.

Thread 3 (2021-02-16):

Create current monitoring PCB

antevens, 2021-02-16:
Create a PCB Addon to measure current for individual circuits, preferably one that plugs into the existing power sockets

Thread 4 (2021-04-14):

Fix thermal reliefs on addon board solder jumper

antevens, 2021-04-14:
The ground side of the solder jumper for the addon boards doesn't have the proper thermal reliefs.

antevens, 2021-04-26:
Fixed in rev 10

Closed 2021-04-26.

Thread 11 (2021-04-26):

Fix GPIO paths from Raspberry Pi to RJ45 to have adjacent ground pours for EMI/Signal integrity

antevens, 2021-04-26:

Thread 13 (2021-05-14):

Add solder-jumbers to disable channel pairing

antevens, 2021-05-14:
The interconnects between channels in the multistable vibrators and/or onboard switches could be enabled-disabled easily with solder-jumpers to allow independent addon board relay control.

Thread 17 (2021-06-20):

Move power cluster for Raspberri

antevens, 2021-06-20:
The components for the power delivery to the Raspberry should be moved so they aren't underneath the Ethernet or USB connectors since these interfere during reverse mounting

These can probably be moved to where the Open Hardware logo is.

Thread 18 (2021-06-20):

Replace 10M ohm resistor banks with 1M

antevens, 2021-06-20:
RC circuit resistors should be 1M not 10M

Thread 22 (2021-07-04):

Missing ground connection on 5v rail

antevens, 2021-07-04:
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

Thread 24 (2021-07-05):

Find out why the magic smoke left the AC indicator LED

antevens, 2021-07-05:

antevens, 2021-07-06:
Replace with

100nf x2 cap and 1000 ohm resistor

antevens, 2021-07-11:
‎399-11988-ND‎
‎C330C104KBR5TA‎
KEMET
CAP CER 0.1UF 630V X7R RADIAL

antevens, 2021-07-25:
use 680ohm 1/2w resistor instead

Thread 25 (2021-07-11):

Support up to 230V for polarity indicators

antevens, 2021-07-11:
Add note or feature mark about using a 230V bulb/lamp on the AC/DC circuit indicator lights to support both 12v and 230V.

https://www.digikey.com/en/products/filter/panel-indicators-pilot-lights 120-230V

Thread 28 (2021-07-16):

Change all 10M Ohm resistors for multivibrators

antevens, 2021-07-16:
The correct values for the multivibrators are 1M Ohm with 1 uFh resistors

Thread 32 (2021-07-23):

Look into why ON/OFF LEDs for upper/ac bank are reverse

antevens, 2021-07-23:
THE LEDs seem to be reversed when going through the resistor bank

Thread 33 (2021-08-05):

Change layout for Aux buttons

antevens, 2021-08-05:
Buttons need to be set up in pairs, current layout doesn't work.

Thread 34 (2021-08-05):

Clamp down diodes get disconnected with manual buttons

antevens, 2021-08-05:
Switching relays manually causes the clamp down diodes to be disconnected which can cause interference when the spools on the relays de-power and inject a power spike with high voltage. This in turn can cause the MCP packages to reset.

Either switching circuits need to be redesigned or addon-boards and relays need to have their on Zener diodes on the other side of the switches.

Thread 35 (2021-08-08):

Remove extra .dcm file from boatcontrol repository

antevens, 2021-08-08:
A small bug report on the repository: you have two files: boatcontrol/BoatControl.dcm and boatcontrol/boatcontrol.dcm that only differ by case. Mac OS by default uses a case-insensitive filesystem and therefore can't cope with that.

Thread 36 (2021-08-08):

Resolve missing EW30_Push_DPDT  library on opening Kicad Project

antevens, 2021-08-08:
Another bug report: When opening the KiCad project, there's the following complaint: "Alias 'EW30_Push_DPDT' not found in library: ..." KiCad libraries can be a pain...

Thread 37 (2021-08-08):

Review all design parts for 24V (up to 32V for charge currents)

antevens, 2021-08-08:
I'm a bit confused about the nominal voltages of the PCB. It's stated that it can be set to run in 12V or 24V mode, but the DC relays would seem to be rated for switching voltages of max. 24V. I think 24V nominal systems should be rated to withstand a continuous voltage of 32V.

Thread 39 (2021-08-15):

Look into moving things around to fit Sailor Hat

antevens, 2021-08-15:
The supercap part of the Sailor Hat interferes with the heatsink on the board

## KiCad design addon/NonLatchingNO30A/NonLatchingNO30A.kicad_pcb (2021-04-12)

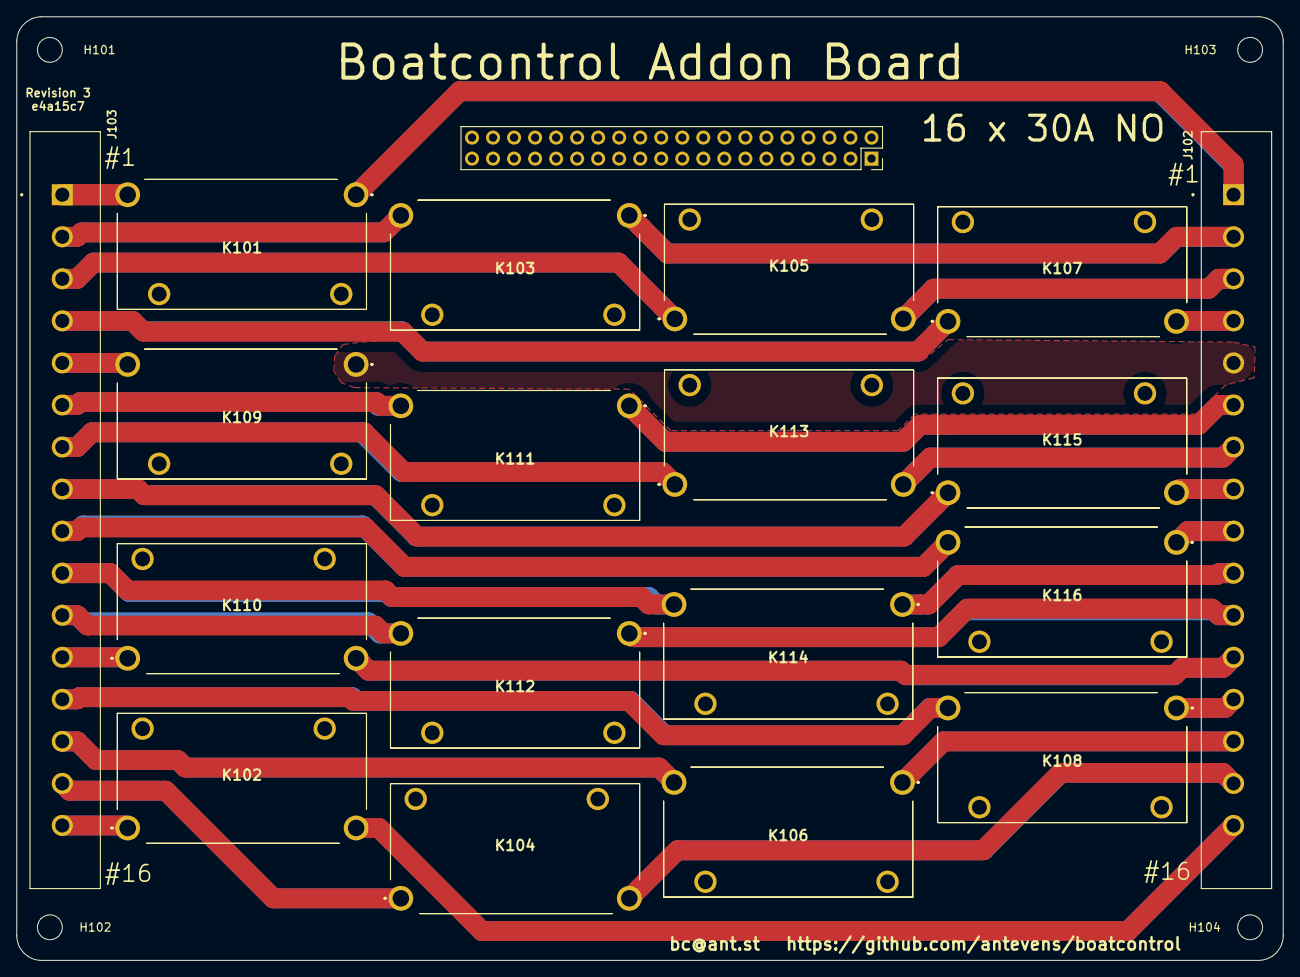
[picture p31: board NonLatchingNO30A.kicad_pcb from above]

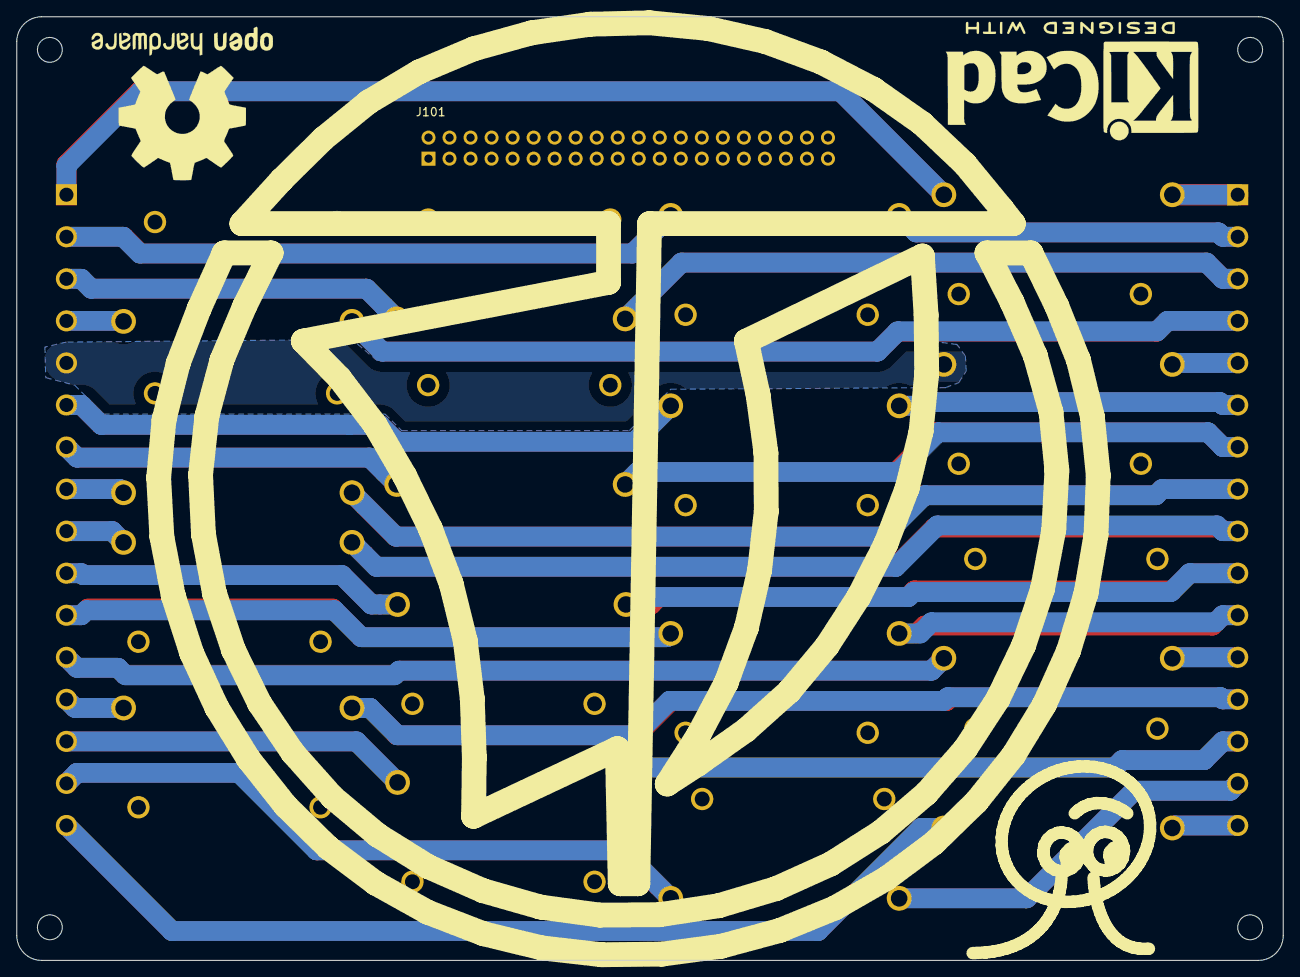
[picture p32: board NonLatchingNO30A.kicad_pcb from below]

Board: 4 copper layers, 153.0 x 114.0 mm, 27 parts (4 on the bottom side), 49 nets.

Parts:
G101: LOGO_RUGLUDALLUR; Rugludallur-Logo_SilkScreen
G102: LOGO_ANT; Ant_Logo_SilkScreen
H101, H102, H103, H104: MountingHole; MountingHole_3mm
J101: Conn_02x20_Odd_Even Header; PinSocket_2x20_P2.54mm_Vertical
J102, J103: TBP01R2W-508-16BE; CUI_TBP01R2W-508-16BE
K101, K102, K103, K104, K105, K106, K107, K108, K109, K110, K111, K112, K113, K114, K115, K116: ALFG2PF121
LOGO101: Logo_Open_Hardware_Large; KiCad-Logo2_12mm_SilkScreen
LOGO102: Logo_Open_Hardware_Large; OSHW-Logo2_24.3x20mm_SilkScreen

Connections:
/K1_COIL_ON: J101.1, J101.2, K101.4
/K2_COIL_ON: J101.3, J101.4, K103.4
/K3_COIL_ON: J101.5, J101.6, K105.3
/K4_COIL_ON: J101.7, J101.8, K107.3
/K5_COIL_ON: J101.9, J101.10, K109.4
/K6_COIL_ON: J101.11, J101.12, K111.4
/K7_COIL_ON: J101.13, J101.14, K113.3
/K8_COIL_ON: J101.15, J101.16, K115.3
/K9_COIL_ON: J101.17, J101.18, K116.4
/K10_COIL_ON: J101.19, J101.20, K114.4
/K11_COIL_ON: J101.21, J101.22, K112.4
/K12_COIL_ON: J101.23, J101.24, K110.3
/K13_COIL_ON: J101.25, J101.26, K108.4
/K14_COIL_ON: J101.27, J101.28, K106.4
/K15_COIL_ON: J101.29, J101.30, K104.3
/K16_COIL_ON: J101.31, J101.32, K102.3
GND: J101.33, J101.34, J101.35, J101.36, J101.37, J101.38, J101.39, J101.40, K101.3, K102.4, K103.3, K104.4, K105.4, K106.3, K107.4, K108.3, K109.3, K110.4, K111.3, K112.3, K113.4, K114.3, K115.4, K116.3
unnamed: J102.1, K101.1
unnamed: J102.2, K103.1
unnamed: J102.3, K105.2
unnamed: J102.4, K107.2
unnamed: J102.5, K109.1
unnamed: J102.6, K111.1
unnamed: J102.7, K113.2
unnamed: J102.8, K115.2
unnamed: J102.9, K116.1
unnamed: J102.10, K114.1
unnamed: J102.11, K112.1
unnamed: J102.12, K110.2
unnamed: J102.13, K108.1
unnamed: J102.14, K106.1
unnamed: J102.15, K104.2
unnamed: J102.16, K102.2
unnamed: J103.1, K101.2
unnamed: J103.2, K103.2
unnamed: J103.3, K105.1
unnamed: J103.4, K107.1
unnamed: J103.5, K109.2
unnamed: J103.6, K111.2
unnamed: J103.7, K113.1
unnamed: J103.8, K115.1
unnamed: J103.9, K116.2
unnamed: J103.10, K114.2
unnamed: J103.11, K112.2
unnamed: J103.12, K110.1
unnamed: J103.13, K108.2
unnamed: J103.14, K106.2
unnamed: J103.15, K104.1
unnamed: J103.16, K102.1

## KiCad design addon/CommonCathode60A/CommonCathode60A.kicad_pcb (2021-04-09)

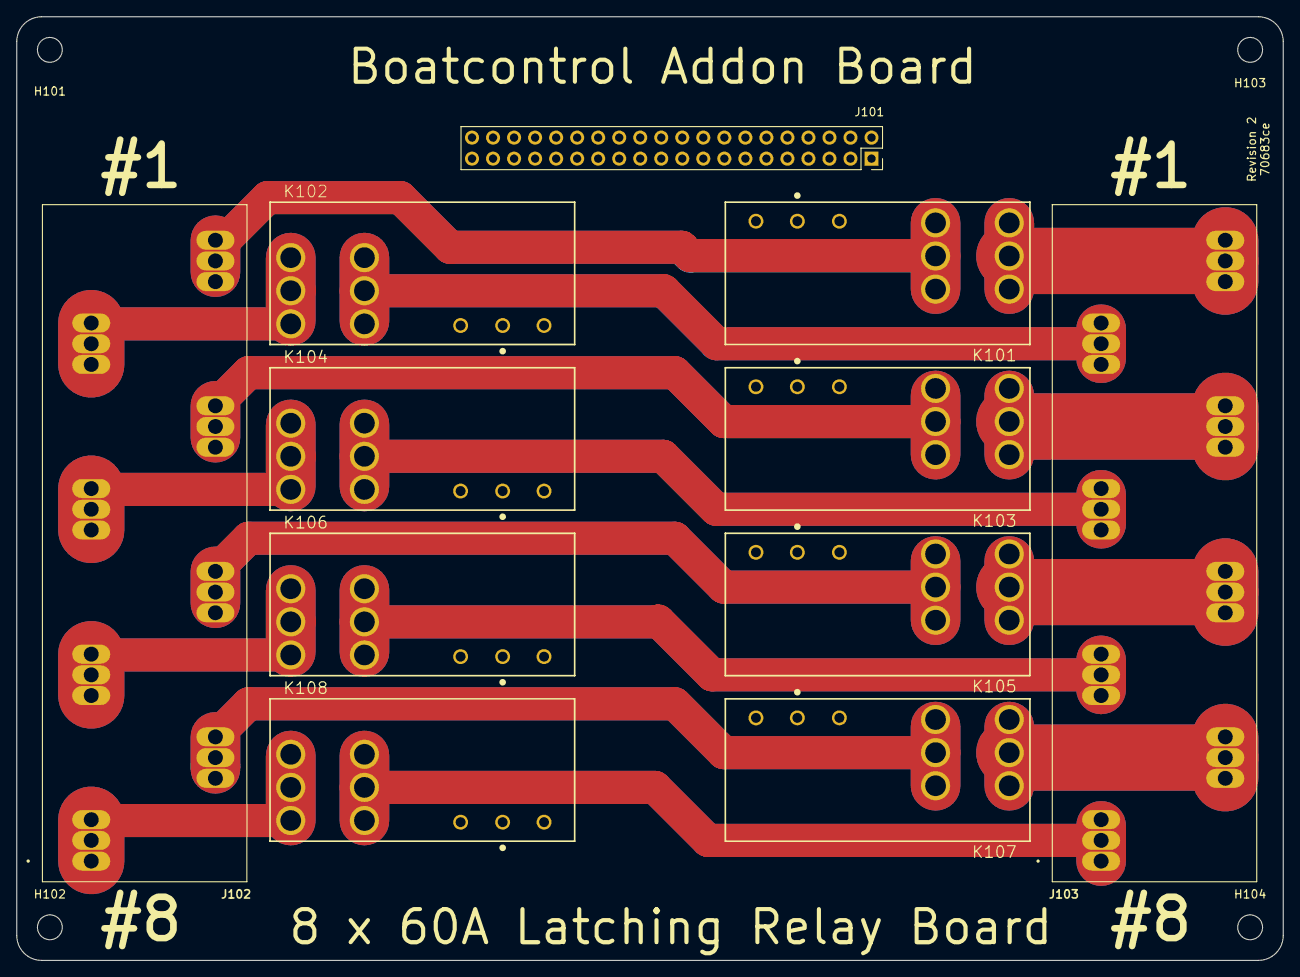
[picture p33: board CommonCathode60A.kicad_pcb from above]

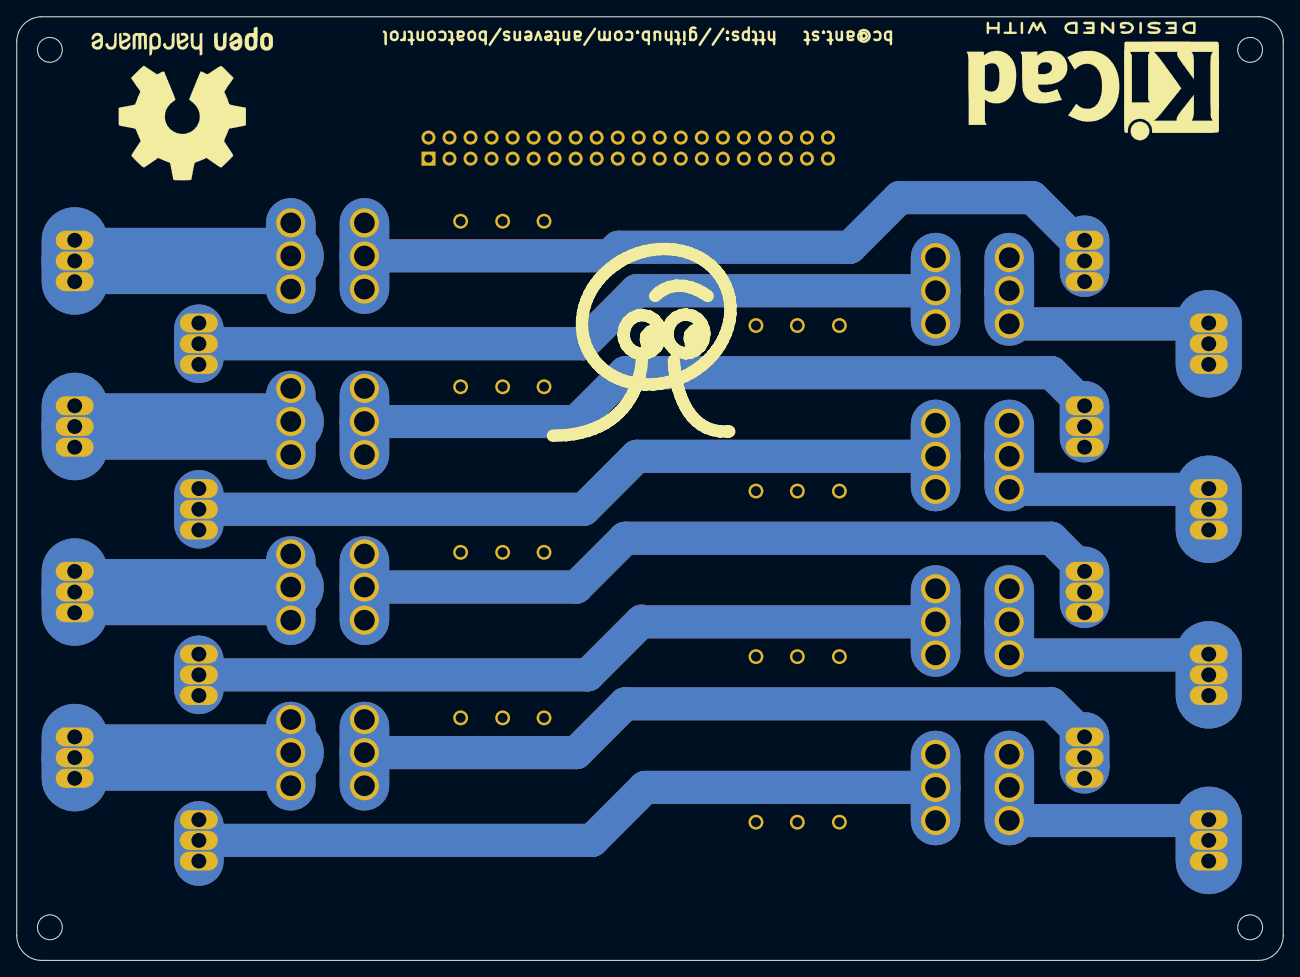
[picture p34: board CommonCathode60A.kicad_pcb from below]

Board: 4 copper layers, 153.0 x 114.0 mm, 18 parts (3 on the bottom side), 33 nets.

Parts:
G102: LOGO_ANT; Ant_Logo_SilkScreen
H101, H102, H103, H104: MountingHole; MountingHole_3mm
J101: Conn_02x20_Odd_Even Header; PinSocket_2x20_P2.54mm_Vertical
J102, J103: TBL008V-1000-08BE; CUI_TBL008V-1000-08BE
K101, K102, K103, K104, K105, K106, K107, K108: EW60-1A3-CL12D04; TE_2071366-2
LOGO101: Logo_Open_Hardware_Large; KiCad-Logo2_12mm_SilkScreen
LOGO102: Logo_Open_Hardware_Large; OSHW-Logo2_24.3x20mm_SilkScreen

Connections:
/K1_COIL_OFF: J101.3, J101.4, K101.A2
/K1_COIL_ON: J101.1, J101.2, K101.A3
/K1_IN: J102.8_1, J102.8_2, J102.8_3, K101.4, K101.5, K101.6
/K1_OUT: J103.8_1, J103.8_2, J103.8_3, K101.1, K101.2, K101.3
/K2_COIL_OFF: J101.7, J101.8, K102.A3
/K2_COIL_ON: J101.5, J101.6, K102.A2
/K2_IN: J102.7_1, J102.7_2, J102.7_3, K102.1, K102.2, K102.3
/K2_OUT: J103.7_1, J103.7_2, J103.7_3, K102.4, K102.5, K102.6
/K3_COIL_OFF: J101.11, J101.12, K103.A2
/K3_COIL_ON: J101.9, J101.10, K103.A3
/K3_IN: J102.6_1, J102.6_2, J102.6_3, K103.4, K103.5, K103.6
/K3_OUT: J103.6_1, J103.6_2, J103.6_3, K103.1, K103.2, K103.3
/K4_COIL_OFF: J101.15, J101.16, K104.A3
/K4_COIL_ON: J101.13, J101.14, K104.A2
/K4_IN: J102.5_1, J102.5_2, J102.5_3, K104.1, K104.2, K104.3
/K4_OUT: J103.5_1, J103.5_2, J103.5_3, K104.4, K104.5, K104.6
/K5_COIL_OFF: J101.19, J101.20, K105.A2
/K5_COIL_ON: J101.17, J101.18, K105.A3
/K5_IN: J102.4_1, J102.4_2, J102.4_3, K105.4, K105.5, K105.6
/K5_OUT: J103.4_1, J103.4_2, J103.4_3, K105.1, K105.2, K105.3
/K6_COIL_OFF: J101.23, J101.24, K106.A3
/K6_COIL_ON: J101.21, J101.22, K106.A2
/K6_IN: J102.3_1, J102.3_2, J102.3_3, K106.1, K106.2, K106.3
/K6_OUT: J103.3_1, J103.3_2, J103.3_3, K106.4, K106.5, K106.6
/K7_COIL_OFF: J101.27, J101.28, K107.A2
/K7_COIL_ON: J101.25, J101.26, K107.A3
/K7_IN: J102.2_1, J102.2_2, J102.2_3, K107.4, K107.5, K107.6
/K7_OUT: J103.2_1, J103.2_2, J103.2_3, K107.1, K107.2, K107.3
/K8_COIL_OFF: J101.31, J101.32, K108.A3
/K8_COIL_ON: J101.29, J101.30, K108.A2
/K8_IN: J102.1_1, J102.1_2, J102.1_3, K108.1, K108.2, K108.3
/K8_OUT: J103.1_1, J103.1_2, J103.1_3, K108.4, K108.5, K108.6
GND: J101.33, J101.34, J101.35, J101.36, J101.37, J101.38, J101.39, J101.40, K101.A1, K102.A1, K103.A1, K104.A1, K105.A1, K106.A1, K107.A1, K108.A1

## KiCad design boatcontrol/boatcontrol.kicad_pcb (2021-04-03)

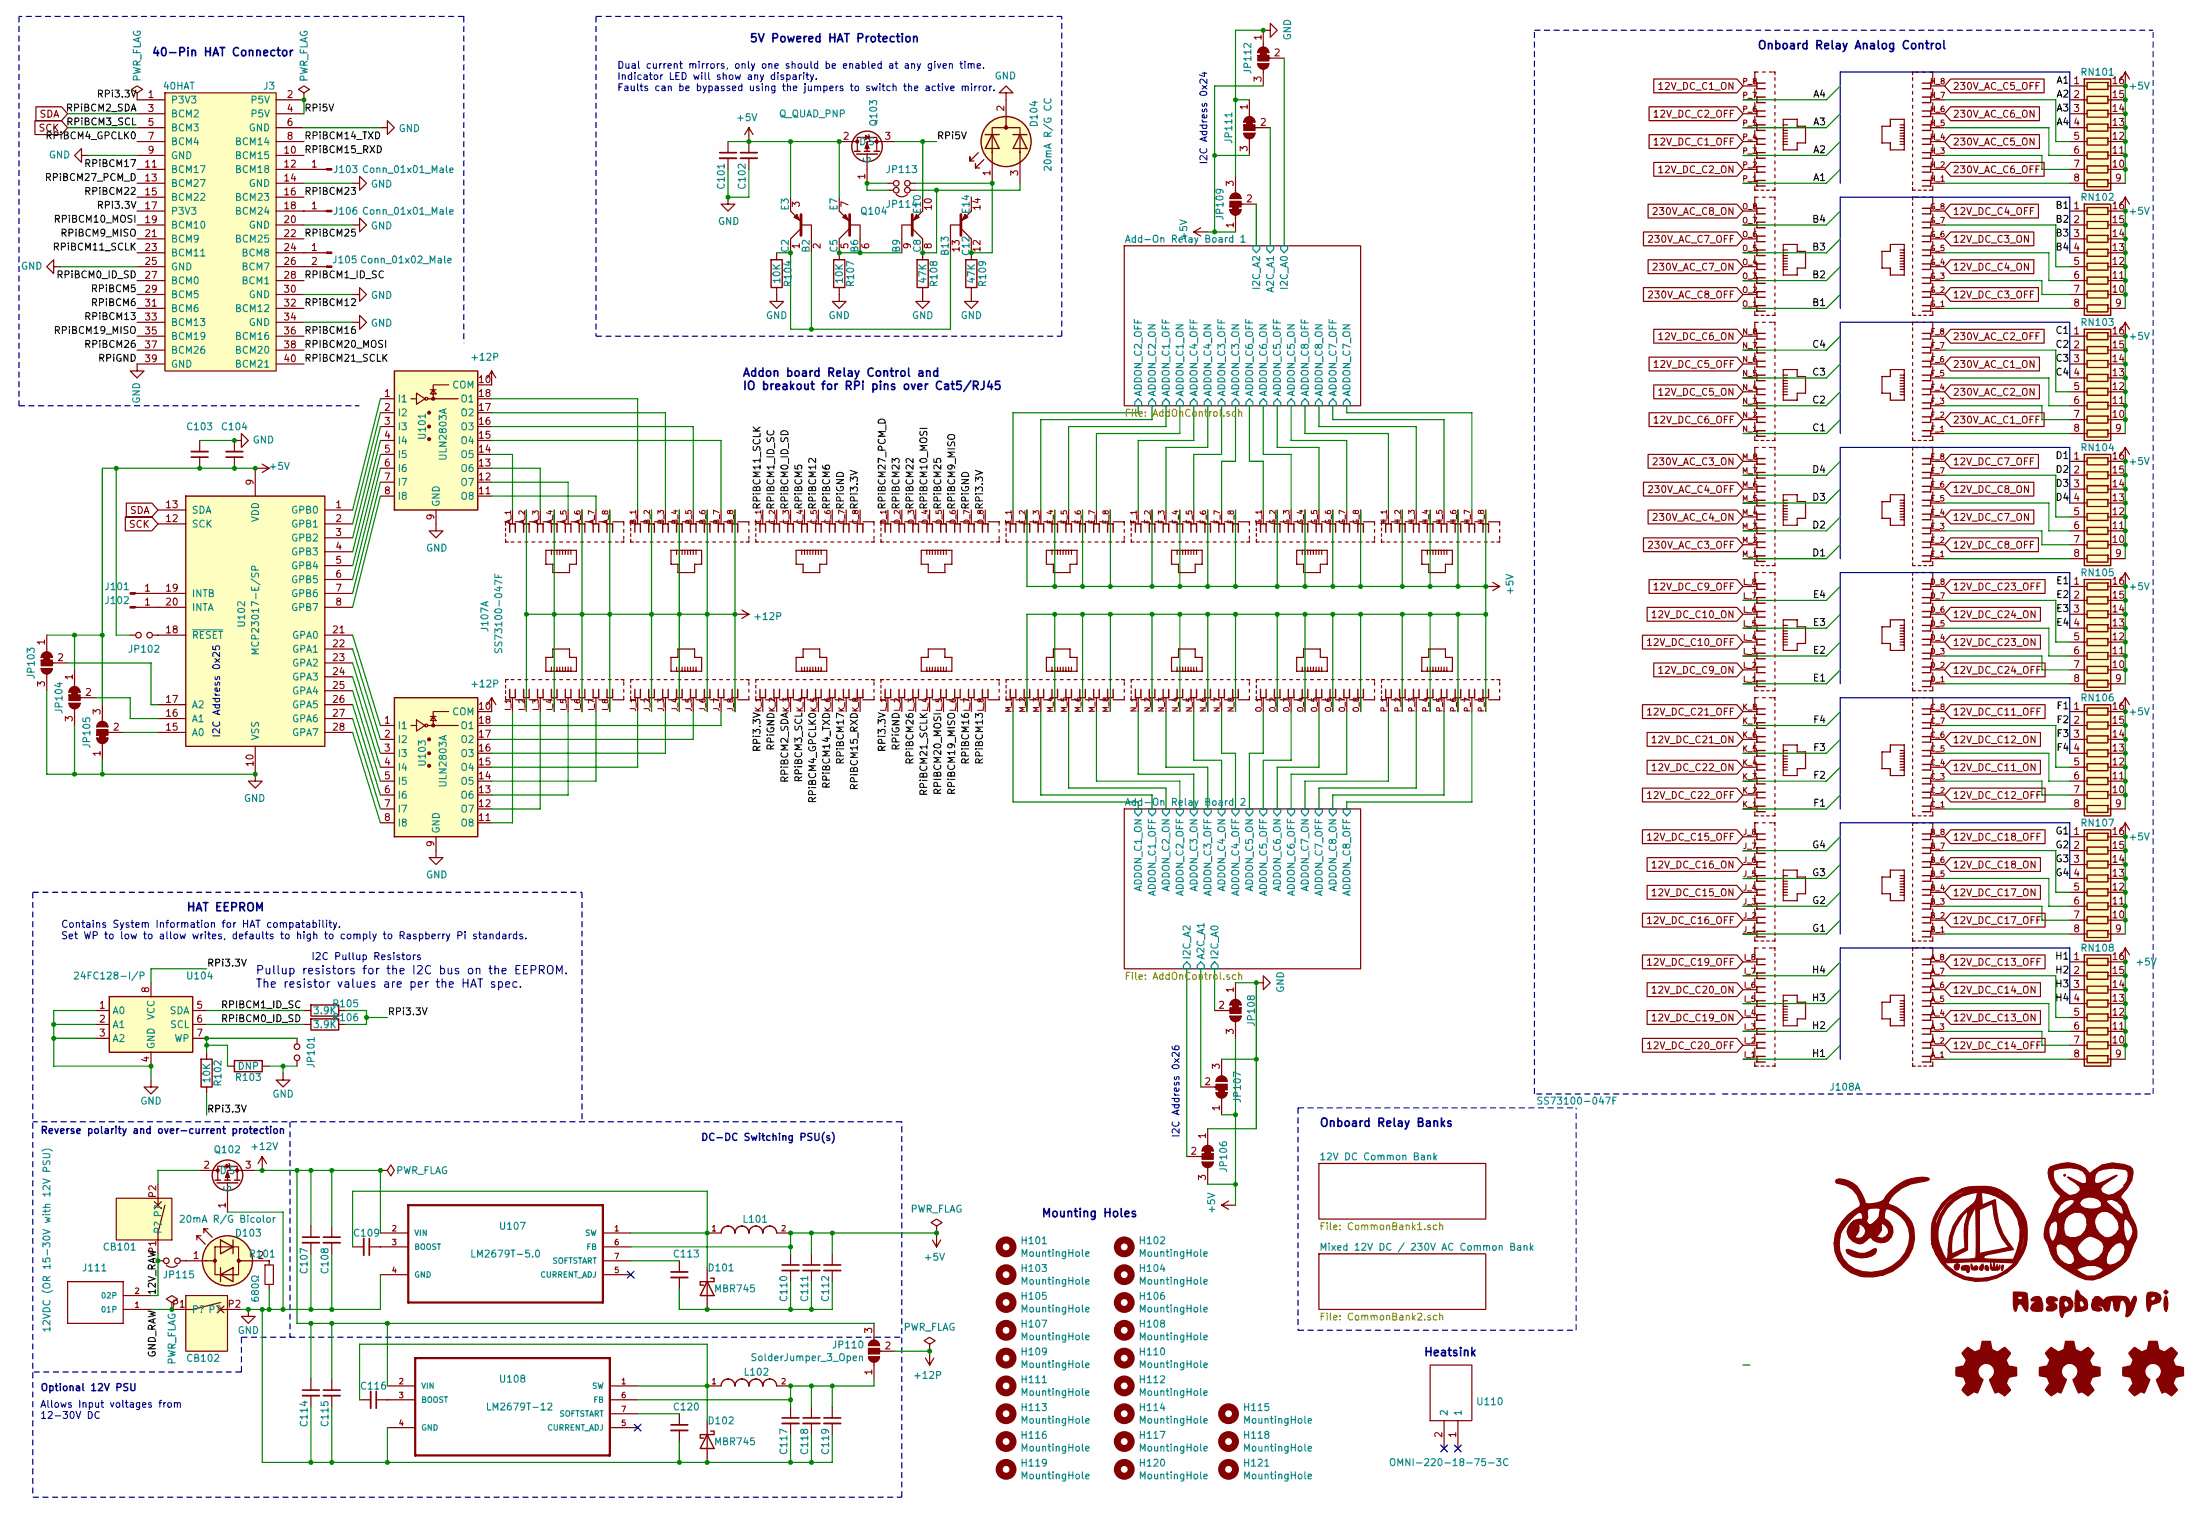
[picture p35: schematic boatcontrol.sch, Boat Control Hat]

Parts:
C101, C112, C119: 10uF; CP_Radial_D8.0mm_P5.00mm
C102: 0.1uF; CP_Radial_D8.0mm_P5.00mm
C103: 10uF; C_Disc_D7.5mm_W5.0mm_P5.00mm
C104: 0.1uF; C_Disc_D7.5mm_W5.0mm_P5.00mm
C107, C114: Illinois Capacitor; CP_Radial_D10.0mm_P5.00mm
C108, C111, C115, C118: 0.22uF; CP_Radial_D8.0mm_P5.00mm
C109, C116: C320C103K1R5TA; CP_Radial_D5.0mm_P2.50mm
C110, C117: 330UF; CP_Radial_D10.0mm_P5.00mm
C113: C315C102K1R5TA7301; CP_Radial_D5.0mm_P2.50mm
C120: C315C272K1R5TA; CP_Radial_D5.0mm_P2.50mm
CB101, CB102: SchurterCircuitBreaker 3a; Schurter_Circuit_Breaker
D101, D102: MBR745; TO-220
D103: 20mA R/G Bicolor; LED_D5.0mm
D104: 20mA R/G CC; LED_D5.0mm-3
G101: LOGO_ANT; Ant_Logo_SilkScreen
G102: LOGO_RUGLUDALLUR; Rugludallur-Logo_SilkScreen
G104: LOGO_RPI; RPi_Logo_SilkScreen
H101, H102, H103, H104, H105, H106, H107, H108, H109, H110, H111, H112, H113, H114, H115, H116, H117, H118, H119, H120, H121: MountingHole; MountingHole_3mm
J3: 40HAT; Raspberry_Pi_Any_Socketed_THT_FaceDown_MountingHoles
J101, J102: Conn_01x01_Male; PinHeader_1x01_P2.54mm_Vertical
J103, J106: Conn_01x01_Male; PinHeader_1x01_P2.00mm_Vertical
J105: Conn_01x02_Male; PinHeader_1x02_P2.00mm_Vertical
J107, J108: SS73100-047F; STEWART_SS73100-047F
J111: TBL008V-1000-02BE; CUI_TBP02R2W-381-02BE
JP101, JP102, JP113: Jumper_NO_Small; PinHeader_1x02_P2.54mm_Vertical
JP103, JP104, JP105, JP106, JP107, JP108, JP109, JP111, JP112: SolderJumper_3_Bridged12; SolderJumper-3_P1.3mm_Bridged12_RoundedPad1.0x1.5mm
JP110: SolderJumper_3_Open; SolderJumper-3_P1.3mm_Open_RoundedPad3.0x4.5mm_NumberLabels
JP114, JP115: Jumper_NC_Small; PinHeader_1x02_P2.54mm_Vertical
L101: 15µH; L_Toroid_Horizontal_Vertical_2103-RC_P19.403mm_Bourns_2100
L102: 10µH; L_Toroid_Horizontal_Vertical_2000-100-RC_P14.244mm_Bourns_2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
LOGO101: Open Hardware; OSHW-Logo2_48.7x40mm_SilkScreen
LOGO102: Logo_Open_Hardware_Small; KiCad-Logo2_40mm_SilkScreen
LOGO103: Logo_Open_Hardware_Small; OSHW-Logo_38.1x40mm_SilkScreen
Q102, Q103: IPP120P04P4L-03; TO-220-3_Vertical
Q104: Q_QUAD_PNP; DIP-14_W7.62mm
R101: 680Ω; R_Axial_DIN0207_L6.3mm_D2.5mm_P7.62mm_Horizontal
R102, R104, R107: 10K; R_Axial_DIN0207_L6.3mm_D2.5mm_P7.62mm_Horizontal
R103: DNP; R_Axial_DIN0207_L6.3mm_D2.5mm_P7.62mm_Horizontal
R105, R106: 3.9K; R_Axial_DIN0207_L6.3mm_D2.5mm_P7.62mm_Horizontal
R108, R109: 47K; R_Axial_DIN0207_L6.3mm_D2.5mm_P7.62mm_Horizontal
RN101, RN102, RN103, RN104, RN105, RN106, RN107, RN108: 10KΩ; SOIC-16W_5.3x10.2mm_P1.27mm; Manufacturer_Part_Number 4816P-103LF-ND
U101, U103: ULN2803A; DIP-18_W7.62mm
U102: MCP23017-E/SP; DIP-28_W7.62mm
U104: 24FC128-I/P; DIP-8_W7.62mm
U107: LM2679T-5.0; TO-220-7_P2.54x3.7mm_StaggerOdd_Lead3.8mm_Vertical
U108: LM2679T-12; TO-220-7_P2.54x3.7mm_StaggerOdd_Lead3.8mm_Vertical
U110: OMNI-220-18-75-3C; OMNI22018753C; Manufacturer_Part_Number OMNI-220-18-75-3C; Mouser Part Number 567-OMNI220-18-75-3C

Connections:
12V_DC_C3_OFF: J108.G_2 (2); also elsewhere on the board
12V_DC_C3_ON: J108.G_6 (6); also elsewhere on the board
12V_DC_C4_OFF: J108.G_8 (8); also elsewhere on the board
12V_DC_C4_ON: J108.G_4 (4); also elsewhere on the board
12V_DC_C5_OFF: J108.N_6 (6); also elsewhere on the board
12V_DC_C5_ON: J108.N_4 (4); also elsewhere on the board
12V_DC_C6_OFF: J108.N_2 (2); also elsewhere on the board
12V_DC_C6_ON: J108.N_8 (8); also elsewhere on the board
12V_DC_C7_OFF: J108.E_8 (8); also elsewhere on the board
12V_DC_C7_ON: J108.E_4 (4); also elsewhere on the board
12V_DC_C8_OFF: J108.E_2 (2); also elsewhere on the board
12V_DC_C8_ON: J108.E_6 (6); also elsewhere on the board
12V_DC_C9_OFF: J108.L_8 (8); also elsewhere on the board
12V_DC_C9_ON: J108.L_2 (2); also elsewhere on the board
12V_DC_C10_OFF: J108.L_4 (4); also elsewhere on the board
12V_DC_C10_ON: J108.L_6 (6); also elsewhere on the board
12V_DC_C13_OFF: J108.A_8 (8); also elsewhere on the board
12V_DC_C13_ON: J108.A_4 (4); also elsewhere on the board
12V_DC_C14_OFF: J108.A_2 (2); also elsewhere on the board
12V_DC_C14_ON: J108.A_6 (6); also elsewhere on the board
12V_DC_C15_OFF: J108.J_8 (8); also elsewhere on the board
12V_DC_C15_ON: J108.J_4 (4); also elsewhere on the board
12V_DC_C16_OFF: J108.J_2 (2); also elsewhere on the board
12V_DC_C16_ON: J108.J_6 (6); also elsewhere on the board
12V_DC_C17_OFF: J108.B_2 (2); also elsewhere on the board
12V_DC_C17_ON: J108.B_4 (4); also elsewhere on the board
12V_DC_C18_OFF: J108.B_8 (8); also elsewhere on the board
12V_DC_C18_ON: J108.B_6 (6); also elsewhere on the board
12V_DC_C19_OFF: J108.I_8 (8); also elsewhere on the board
12V_DC_C19_ON: J108.I_4 (4); also elsewhere on the board
12V_DC_C20_OFF: J108.I_2 (2); also elsewhere on the board
12V_DC_C20_ON: J108.I_6 (6); also elsewhere on the board
12V_DC_C21_OFF: J108.K_8 (8); also elsewhere on the board
12V_DC_C21_ON: J108.K_6 (6); also elsewhere on the board
12V_DC_C22_OFF: J108.K_2 (2); also elsewhere on the board
12V_DC_C22_ON: J108.K_4 (4); also elsewhere on the board
12V_DC_C23_OFF: J108.D_8 (8); also elsewhere on the board
12V_DC_C23_ON: J108.D_4 (4); also elsewhere on the board
12V_DC_C24_OFF: J108.D_2 (2); also elsewhere on the board
12V_DC_C24_ON: J108.D_6 (6); also elsewhere on the board
230V_AC_C1_OFF: J108.F_2 (2); also elsewhere on the board
230V_AC_C1_ON: J108.F_6 (6); also elsewhere on the board
230V_AC_C2_OFF: J108.F_8 (8); also elsewhere on the board
230V_AC_C2_ON: J108.F_4 (4); also elsewhere on the board
230V_AC_C3_OFF: J108.M_2 (2); also elsewhere on the board
230V_AC_C3_ON: J108.M_8 (8); also elsewhere on the board
230V_AC_C4_OFF: J108.M_6 (6); also elsewhere on the board
230V_AC_C4_ON: J108.M_4 (4); also elsewhere on the board
230V_AC_C5_OFF: J108.H_8 (8); also elsewhere on the board
230V_AC_C5_ON: J108.H_4 (4); also elsewhere on the board
230V_AC_C6_OFF: J108.H_2 (2); also elsewhere on the board
230V_AC_C6_ON: J108.H_6 (6); also elsewhere on the board
230V_AC_C7_OFF: J108.O_6 (6); also elsewhere on the board
230V_AC_C7_ON: J108.O_4 (4); also elsewhere on the board
230V_AC_C8_OFF: J108.O_2 (2); also elsewhere on the board
230V_AC_C8_ON: J108.O_8 (8); also elsewhere on the board
+5V: C101.1, C102.1, C103.1, C104.1, C110.1, C111.1, C112.1, J107.E_2 (2), J107.E_4 (4), J107.E_6 (6), J107.E_8 (8), J107.F_2 (2), J107.F_4 (4), J107.F_6 (6), J107.F_8 (8), J107.G_2 (2), J107.G_4 (4), J107.G_6 (6), J107.G_8 (8), J107.H_2 (2), J107.H_4 (4), J107.H_6 (6), J107.H_8 (8), J107.M_2 (2), J107.M_4 (4), J107.M_6 (6), J107.M_8 (8), J107.N_2 (2), J107.N_4 (4), J107.N_6 (6), J107.N_8 (8), J107.O_2 (2), J107.O_4 (4), J107.O_6 (6), J107.O_8 (8), J107.P_2 (2), J107.P_4 (4), J107.P_6 (6), J107.P_8 (8), JP102.2, JP103.1 (A), JP104.1 (A), JP105.3 (B), JP106.3 (B), JP107.1 (A), JP108.3 (B), JP109.1 (A), JP111.3 (B), JP112.3 (B), L101.2, Q103.2 (D), Q104.3 (E3), Q104.7 (E7), RN101.9 (R8.2), RN101.10 (R7.2), RN101.11 (R6.2), RN101.12 (R5.2), RN101.13 (R4.2), RN101.14 (R3.2), RN101.15 (R2.2), RN101.16 (R1.2), RN102.9 (R8.2), RN102.10 (R7.2), RN102.11 (R6.2), RN102.12 (R5.2), RN102.13 (R4.2), RN102.14 (R3.2), RN102.15 (R2.2), RN102.16 (R1.2), RN103.9 (R8.2), RN103.10 (R7.2), RN103.11 (R6.2), RN103.12 (R5.2), RN103.13 (R4.2), RN103.14 (R3.2), RN103.15 (R2.2), RN103.16 (R1.2), RN104.9 (R8.2), RN104.10 (R7.2), RN104.11 (R6.2), RN104.12 (R5.2), RN104.13 (R4.2), RN104.14 (R3.2), RN104.15 (R2.2), RN104.16 (R1.2), RN105.9 (R8.2), RN105.10 (R7.2), RN105.11 (R6.2), RN105.12 (R5.2), RN105.13 (R4.2), RN105.14 (R3.2), RN105.15 (R2.2), RN105.16 (R1.2), RN106.9 (R8.2), RN106.10 (R7.2), RN106.11 (R6.2), RN106.12 (R5.2), RN106.13 (R4.2), RN106.14 (R3.2), RN106.15 (R2.2), RN106.16 (R1.2), RN107.9 (R8.2), RN107.10 (R7.2), RN107.11 (R6.2), RN107.12 (R5.2), RN107.13 (R4.2), RN107.14 (R3.2), RN107.15 (R2.2), RN107.16 (R1.2), RN108.9 (R8.2), RN108.10 (R7.2), RN108.11 (R6.2), RN108.12 (R5.2), RN108.13 (R4.2), RN108.14 (R3.2), RN108.15 (R2.2), RN108.16 (R1.2), U102.9 (VDD), U107.6 (FB); also elsewhere on the board
+12P: J107.A_2 (2), J107.A_4 (4), J107.A_6 (6), J107.A_8 (8), J107.B_2 (2), J107.B_4 (4), J107.B_6 (6), J107.B_8 (8), J107.I_2 (2), J107.I_4 (4), J107.I_6 (6), J107.I_8 (8), J107.J_2 (2), J107.J_4 (4), J107.J_6 (6), J107.J_8 (8), JP110.2 (C), U101.10 (COM), U103.10 (COM); also elsewhere on the board
+12V: C107.1, C108.1, C114.1, C115.1, JP110.3 (B), Q102.3 (S), U107.2 (VIN), U108.2 (VIN)
/12V_RAW: CB101.P1, J111.2 (02P), JP115.2
/A1: J108.P_1 (1), RN101.1 (R1.1)
/A2: J108.P_3 (3), RN101.2 (R2.1)
/A3: J108.P_5 (5), RN101.3 (R3.1)
/A4: J108.P_7 (7), RN101.4 (R4.1)
/Add-On Relay Board 1/A2C_A1: JP111.2 (C); also elsewhere on the board
/Add-On Relay Board 1/ADDON_C1_OFF: J107.E_5 (5); also elsewhere on the board
/Add-On Relay Board 1/ADDON_C1_ON: J107.E_7 (7); also elsewhere on the board
/Add-On Relay Board 1/ADDON_C2_OFF: J107.E_1 (1); also elsewhere on the board
/Add-On Relay Board 1/ADDON_C2_ON: J107.E_3 (3); also elsewhere on the board
/Add-On Relay Board 1/ADDON_C3_OFF: J107.F_5 (5); also elsewhere on the board
/Add-On Relay Board 1/ADDON_C3_ON: J107.F_7 (7); also elsewhere on the board
/Add-On Relay Board 1/ADDON_C4_OFF: J107.F_1 (1); also elsewhere on the board
/Add-On Relay Board 1/ADDON_C4_ON: J107.F_3 (3); also elsewhere on the board
/Add-On Relay Board 1/ADDON_C5_OFF: J107.G_5 (5); also elsewhere on the board
/Add-On Relay Board 1/ADDON_C5_ON: J107.G_7 (7); also elsewhere on the board
/Add-On Relay Board 1/ADDON_C6_OFF: J107.G_1 (1); also elsewhere on the board
/Add-On Relay Board 1/ADDON_C6_ON: J107.G_3 (3); also elsewhere on the board
/Add-On Relay Board 1/ADDON_C7_OFF: J107.H_5 (5); also elsewhere on the board
/Add-On Relay Board 1/ADDON_C7_ON: J107.H_7 (7); also elsewhere on the board
/Add-On Relay Board 1/ADDON_C8_OFF: J107.H_1 (1); also elsewhere on the board
/Add-On Relay Board 1/ADDON_C8_ON: J107.H_3 (3); also elsewhere on the board
/Add-On Relay Board 1/I2C_A0: JP112.2 (C); also elsewhere on the board
/Add-On Relay Board 1/I2C_A2: JP109.2 (C); also elsewhere on the board
/Add-On Relay Board 2/A2C_A1: JP107.2 (C); also elsewhere on the board
/Add-On Relay Board 2/ADDON_C1_OFF: J107.M_3 (3); also elsewhere on the board
/Add-On Relay Board 2/ADDON_C1_ON: J107.M_1 (1); also elsewhere on the board
/Add-On Relay Board 2/ADDON_C2_OFF: J107.M_7 (7); also elsewhere on the board
/Add-On Relay Board 2/ADDON_C2_ON: J107.M_5 (5); also elsewhere on the board
/Add-On Relay Board 2/ADDON_C3_OFF: J107.N_3 (3); also elsewhere on the board
/Add-On Relay Board 2/ADDON_C3_ON: J107.N_1 (1); also elsewhere on the board
/Add-On Relay Board 2/ADDON_C4_OFF: J107.N_7 (7); also elsewhere on the board
/Add-On Relay Board 2/ADDON_C4_ON: J107.N_5 (5); also elsewhere on the board
/Add-On Relay Board 2/ADDON_C5_OFF: J107.O_3 (3); also elsewhere on the board
/Add-On Relay Board 2/ADDON_C5_ON: J107.O_1 (1); also elsewhere on the board
/Add-On Relay Board 2/ADDON_C6_OFF: J107.O_7 (7); also elsewhere on the board
/Add-On Relay Board 2/ADDON_C6_ON: J107.O_5 (5); also elsewhere on the board
/Add-On Relay Board 2/ADDON_C7_OFF: J107.P_3 (3); also elsewhere on the board
/Add-On Relay Board 2/ADDON_C7_ON: J107.P_1 (1); also elsewhere on the board
/Add-On Relay Board 2/ADDON_C8_OFF: J107.P_7 (7); also elsewhere on the board
/Add-On Relay Board 2/ADDON_C8_ON: J107.P_5 (5); also elsewhere on the board
/Add-On Relay Board 2/I2C_A0: JP108.2 (C); also elsewhere on the board
/Add-On Relay Board 2/I2C_A2: JP106.2 (C); also elsewhere on the board
/B1: J108.O_1 (1), RN102.1 (R1.1)
/B2: J108.O_3 (3), RN102.2 (R2.1)
/B3: J108.O_5 (5), RN102.3 (R3.1)
/B4: J108.O_7 (7), RN102.4 (R4.1)
/C1: J108.N_1 (1), RN103.1 (R1.1)
/C2: J108.N_3 (3), RN103.2 (R2.1)
/C3: J108.N_5 (5), RN103.3 (R3.1)
/C4: J108.N_7 (7), RN103.4 (R4.1)
/D1: J108.M_1 (1), RN104.1 (R1.1)
/D2: J108.M_3 (3), RN104.2 (R2.1)
/D3: J108.M_5 (5), RN104.3 (R3.1)
/D4: J108.M_7 (7), RN104.4 (R4.1)
/E1: J108.L_1 (1), RN105.1 (R1.1)
/E2: J108.L_3 (3), RN105.2 (R2.1)
/E3: J108.L_5 (5), RN105.3 (R3.1)
/E4: J108.L_7 (7), RN105.4 (R4.1)
/F1: J108.K_1 (1), RN106.1 (R1.1)
/F2: J108.K_3 (3), RN106.2 (R2.1)
/F3: J108.K_5 (5), RN106.3 (R3.1)
/F4: J108.K_7 (7), RN106.4 (R4.1)
/G1: J108.J_1 (1), RN107.1 (R1.1)
/G2: J108.J_3 (3), RN107.2 (R2.1)
/G3: J108.J_5 (5), RN107.3 (R3.1)
/G4: J108.J_7 (7), RN107.4 (R4.1)
/GND_RAW: CB102.P1, J111.1 (01P)
/H1: J108.I_1 (1), RN108.1 (R1.1)
/H2: J108.I_3 (3), RN108.2 (R2.1)
/H3: J108.I_5 (5), RN108.3 (R3.1)
/H4: J108.I_7 (7), RN108.4 (R4.1)
/RPIBCM1_ID_SC: J3.28 (BCM1), J107.C_2 (2), R105.2, U104.5 (SDA)
/RPIBCM20_MOSI: J3.38 (BCM20), J107.L_5 (5)
/RPi3.3V: J3.1 (P3V3), J3.17 (P3V3), J107.C_8 (8), J107.D_8 (8), J107.K_1 (1), J107.L_1 (1), R102.1, R105.1, R106.1, U104.8 (VCC)
/RPi5V: J3.2 (P5V), J3.4 (P5V), Q103.3 (S), Q104.10 (E10)
/RPiBCM0_ID_SD: J3.27 (BCM0), J107.C_3 (3), R106.2, U104.6 (SCL)
/RPiBCM4_GPCLK0: J3.7 (BCM4), J107.K_5 (5)
/RPiBCM5: J3.29 (BCM5), J107.C_4 (4)
/RPiBCM6: J3.31 (BCM6), J107.C_6 (6)
/RPiBCM9_MISO: J3.21 (BCM9), J107.D_6 (6)
/RPiBCM10_MOSI: J3.19 (BCM10), J107.D_4 (4)
/RPiBCM11_SCLK: J3.23 (BCM11), J107.C_1 (1)
/RPiBCM12: J3.32 (BCM12), J107.C_5 (5)
/RPiBCM13: J3.33 (BCM13), J107.L_8 (8)
/RPiBCM14_TXD: J3.8 (BCM14), J107.K_6 (6)
/RPiBCM15_RXD: J3.10 (BCM15), J107.K_8 (8)
/RPiBCM16: J3.36 (BCM16), J107.L_7 (7)
/RPiBCM17: J3.11 (BCM17), J107.K_7 (7)
/RPiBCM19_MISO: J3.35 (BCM19), J107.L_6 (6)
/RPiBCM21_SCLK: J3.40 (BCM21), J107.L_4 (4)
/RPiBCM22: J3.15 (BCM22), J107.D_3 (3)
/RPiBCM23: J3.16 (BCM23), J107.D_2 (2)
/RPiBCM25: J3.22 (BCM25), J107.D_5 (5)
/RPiBCM26: J3.37 (BCM26), J107.L_3 (3)
/RPiBCM27_PCM_D: J3.13 (BCM27), J107.D_1 (1)
GND: C101.2, C102.2, C103.2, C104.2, C107.2, C108.2, C114.2, C115.2, C117.2, C118.2, C119.2, C120.2, CB102.P2, D102.2 (A), D104.2 (K), J3.6 (GND), J3.9 (GND), J3.14 (GND), J3.20 (GND), J3.25 (GND), J3.30 (GND), J3.34 (GND), J3.39 (GND), J107.C_7 (7), J107.D_7 (7), J107.K_2 (2), J107.L_2 (2), JP101.2, JP103.3 (B), JP104.3 (B), JP105.1 (A), JP106.1 (A), JP107.3 (B), JP108.1 (A), JP109.3 (B), JP111.1 (A), JP112.1 (A), Q102.1 (G), R101.2, R103.2, R104.1, R107.1, R108.1, R109.1, U101.9 (GND), U102.10 (VSS), U103.9 (GND), U104.1 (A0), U104.2 (A1), U104.3 (A2), U104.4 (GND), U107.4 (GND), U108.4 (GND); also elsewhere on the board
unnamed: C109.1, U107.3 (BOOST)
unnamed: C109.2, D101.1 (K), L101.1, U107.1 (SW)
unnamed: C110.2, C111.2, C112.2, C113.2, D101.2 (A)
unnamed: C113.1, U107.7 (SOFTSTART)
unnamed: C116.1, U108.3 (BOOST)
unnamed: C116.2, D102.1 (K), L102.1, U108.1 (SW)
unnamed: C117.1, C118.1, C119.1, JP110.1 (A), L102.2, U108.6 (FB)
unnamed: C120.1, U108.7 (SOFTSTART)
unnamed: CB101.P2, Q102.2 (D)
unnamed: D103.1 (KA), JP115.1
unnamed: D103.2 (AK), R101.1
unnamed: D104.1 (A1), JP113.2, Q104.12 (C12), R109.2
unnamed: D104.3 (A2), JP114.1, Q104.8 (C8), R108.2
unnamed: J101.1, U102.19 (INTB)
unnamed: J102.1, U102.20 (INTA)
unnamed: J3.12 (BCM18), J103.1
unnamed: J3.24 (BCM8), J105.1
unnamed: J3.26 (BCM7), J105.2
unnamed: J3.18 (BCM24), J106.1
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

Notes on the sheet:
DC-DC Switching PSU(s)
Reverse polarity and over-current protection
Onboard Relay Banks
Allows Input voltages from 12-30V DC
Optional 12V PSU
Mounting Holes
Contains System Information for HAT compatability. Set WP to low to allow writes, defaults to high to comply to Raspberry Pi standards.
HAT EEPROM
I2C Pullup Resistors
Pullup resistors for the I2C bus on the EEPROM. The resistor values are per the HAT spec.
Dual current mirrors, only one should be enabled at any given time. Indicator LED will show any disparity. Faults can be bypassed using the jumpers to switch the active mirror.
5V Powered HAT Protection
40-Pin HAT Connector
I2C Address 0x25
I2C Address 0x26
Addon board Relay Control and IO breakout for RPi pins over Cat5/RJ45
I2C Address 0x24
Heatsink
Onboard Relay Analog Control

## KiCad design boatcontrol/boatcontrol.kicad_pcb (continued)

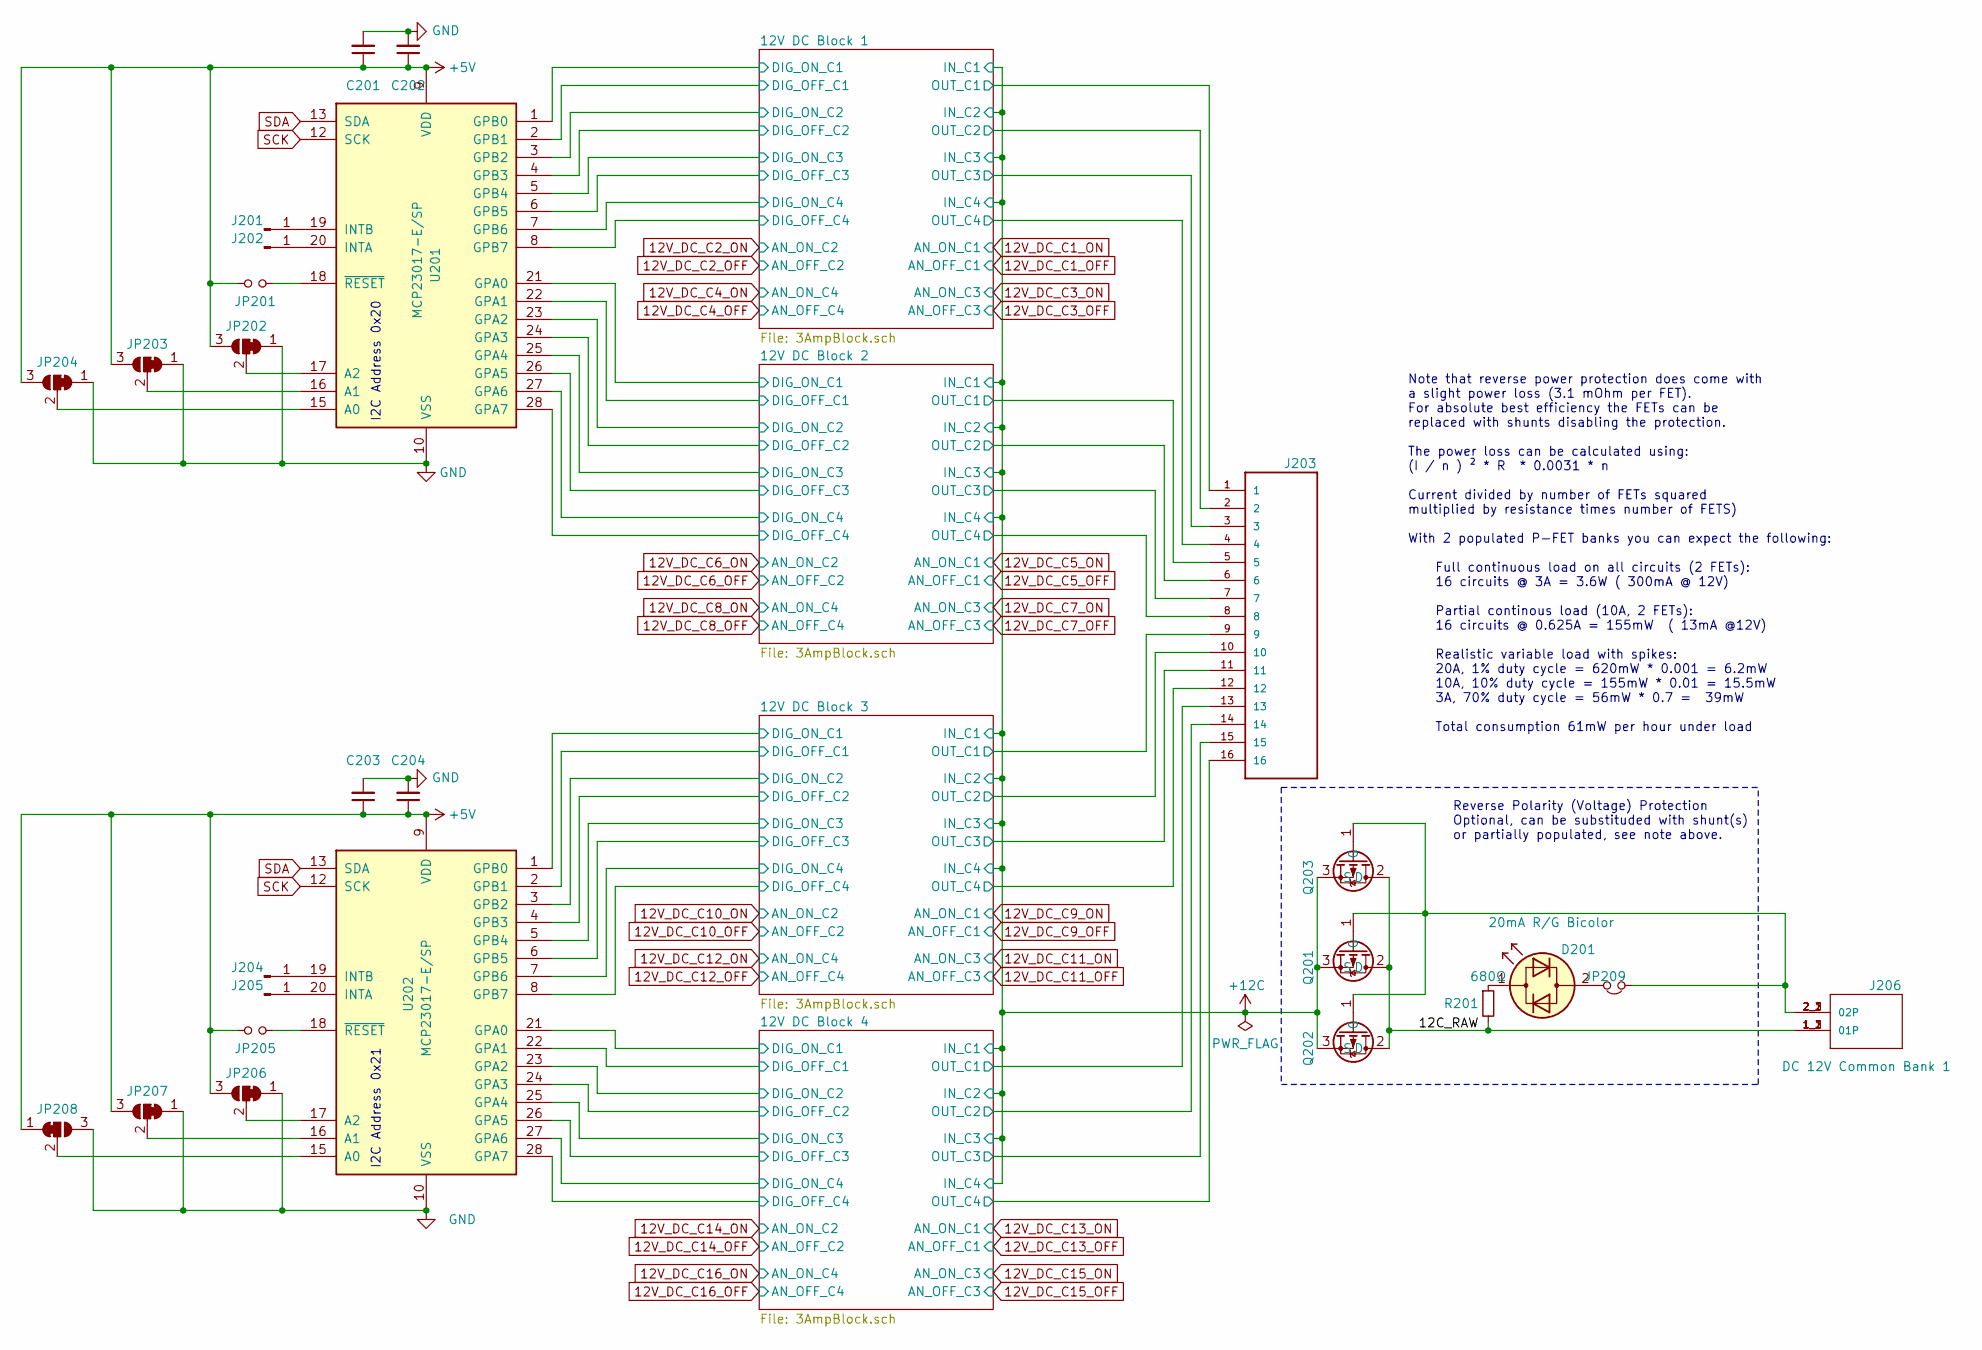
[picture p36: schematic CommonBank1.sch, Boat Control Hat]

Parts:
C201, C203: 10μF; C_Disc_D7.5mm_W5.0mm_P5.00mm
C202, C204: 0.1μF; C_Disc_D7.5mm_W5.0mm_P5.00mm
D201: 20mA R/G Bicolor; LED_D5.0mm
J201, J202, J204, J205: Conn_01x01_Male; PinHeader_1x01_P2.54mm_Vertical
J203: TBP01R2W-508-16BE; CUI_TBP01R2W-508-16BE
J206: TBL008V-1000-02BE; CUI_TBL008V-1000-02BE
JP201, JP205: Jumper_NO_Small; PinHeader_1x02_P2.54mm_Vertical
JP202, JP203, JP204, JP206, JP207, JP208: SolderJumper_3_Bridged12; SolderJumper-3_P1.3mm_Bridged12_RoundedPad1.0x1.5mm
JP209: Jumper_NC_Small; PinHeader_1x02_P2.54mm_Vertical
Q201, Q202, Q203: IPP120P04P4L-03; TO-220-3_Vertical
R201: 680Ω; R_Axial_DIN0207_L6.3mm_D2.5mm_P7.62mm_Horizontal
U201, U202: MCP23017-E/SP; DIP-28_W7.62mm

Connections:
+5V: C201.1, C202.1, C203.1, C204.1, JP201.2, JP202.3 (B), JP203.3 (B), JP204.3 (B), JP205.2, JP206.3 (B), JP207.3 (B), JP208.1 (A), U201.9 (VDD), U202.9 (VDD); also elsewhere on the board
+12C: Q201.3 (S), Q202.3 (S), Q203.3 (S); also elsewhere on the board
/12V DC Common Bank/12C_RAW: J206.1_1 (01P), J206.1_2 (01P), J206.1_3 (01P), Q201.2 (D), Q202.2 (D), Q203.2 (D), R201.2
/12V DC Common Bank/12V DC Block 1/DIG_OFF_C1: U201.2 (GPB1); also elsewhere on the board
/12V DC Common Bank/12V DC Block 1/DIG_OFF_C2: U201.4 (GPB3); also elsewhere on the board
/12V DC Common Bank/12V DC Block 1/DIG_OFF_C3: U201.6 (GPB5); also elsewhere on the board
/12V DC Common Bank/12V DC Block 1/DIG_OFF_C4: U201.8 (GPB7); also elsewhere on the board
/12V DC Common Bank/12V DC Block 1/DIG_ON_C1: U201.1 (GPB0); also elsewhere on the board
/12V DC Common Bank/12V DC Block 1/DIG_ON_C2: U201.3 (GPB2); also elsewhere on the board
/12V DC Common Bank/12V DC Block 1/DIG_ON_C3: U201.5 (GPB4); also elsewhere on the board
/12V DC Common Bank/12V DC Block 1/DIG_ON_C4: U201.7 (GPB6); also elsewhere on the board
/12V DC Common Bank/12V DC Block 1/OUT_C1: J203.1; also elsewhere on the board
/12V DC Common Bank/12V DC Block 1/OUT_C2: J203.2; also elsewhere on the board
/12V DC Common Bank/12V DC Block 1/OUT_C3: J203.3; also elsewhere on the board
/12V DC Common Bank/12V DC Block 1/OUT_C4: J203.4; also elsewhere on the board
/12V DC Common Bank/12V DC Block 2/DIG_OFF_C1: U201.22 (GPA1); also elsewhere on the board
/12V DC Common Bank/12V DC Block 2/DIG_OFF_C2: U201.24 (GPA3); also elsewhere on the board
/12V DC Common Bank/12V DC Block 2/DIG_OFF_C3: U201.26 (GPA5); also elsewhere on the board
/12V DC Common Bank/12V DC Block 2/DIG_OFF_C4: U201.28 (GPA7); also elsewhere on the board
/12V DC Common Bank/12V DC Block 2/DIG_ON_C1: U201.21 (GPA0); also elsewhere on the board
/12V DC Common Bank/12V DC Block 2/DIG_ON_C2: U201.23 (GPA2); also elsewhere on the board
/12V DC Common Bank/12V DC Block 2/DIG_ON_C3: U201.25 (GPA4); also elsewhere on the board
/12V DC Common Bank/12V DC Block 2/DIG_ON_C4: U201.27 (GPA6); also elsewhere on the board
/12V DC Common Bank/12V DC Block 2/OUT_C1: J203.5; also elsewhere on the board
/12V DC Common Bank/12V DC Block 2/OUT_C2: J203.6; also elsewhere on the board
/12V DC Common Bank/12V DC Block 2/OUT_C3: J203.7; also elsewhere on the board
/12V DC Common Bank/12V DC Block 2/OUT_C4: J203.8; also elsewhere on the board
/12V DC Common Bank/12V DC Block 3/DIG_OFF_C1: U202.2 (GPB1); also elsewhere on the board
/12V DC Common Bank/12V DC Block 3/DIG_OFF_C2: U202.4 (GPB3); also elsewhere on the board
/12V DC Common Bank/12V DC Block 3/DIG_OFF_C3: U202.6 (GPB5); also elsewhere on the board
/12V DC Common Bank/12V DC Block 3/DIG_OFF_C4: U202.8 (GPB7); also elsewhere on the board
/12V DC Common Bank/12V DC Block 3/DIG_ON_C1: U202.1 (GPB0); also elsewhere on the board
/12V DC Common Bank/12V DC Block 3/DIG_ON_C2: U202.3 (GPB2); also elsewhere on the board
/12V DC Common Bank/12V DC Block 3/DIG_ON_C3: U202.5 (GPB4); also elsewhere on the board
/12V DC Common Bank/12V DC Block 3/DIG_ON_C4: U202.7 (GPB6); also elsewhere on the board
/12V DC Common Bank/12V DC Block 3/OUT_C1: J203.9; also elsewhere on the board
/12V DC Common Bank/12V DC Block 3/OUT_C2: J203.10; also elsewhere on the board
/12V DC Common Bank/12V DC Block 3/OUT_C3: J203.11; also elsewhere on the board
/12V DC Common Bank/12V DC Block 3/OUT_C4: J203.12; also elsewhere on the board
/12V DC Common Bank/12V DC Block 4/DIG_OFF_C1: U202.22 (GPA1); also elsewhere on the board
/12V DC Common Bank/12V DC Block 4/DIG_OFF_C2: U202.24 (GPA3); also elsewhere on the board
/12V DC Common Bank/12V DC Block 4/DIG_OFF_C3: U202.26 (GPA5); also elsewhere on the board
/12V DC Common Bank/12V DC Block 4/DIG_OFF_C4: U202.28 (GPA7); also elsewhere on the board
/12V DC Common Bank/12V DC Block 4/DIG_ON_C1: U202.21 (GPA0); also elsewhere on the board
/12V DC Common Bank/12V DC Block 4/DIG_ON_C2: U202.23 (GPA2); also elsewhere on the board
/12V DC Common Bank/12V DC Block 4/DIG_ON_C3: U202.25 (GPA4); also elsewhere on the board
/12V DC Common Bank/12V DC Block 4/DIG_ON_C4: U202.27 (GPA6); also elsewhere on the board
/12V DC Common Bank/12V DC Block 4/OUT_C1: J203.13; also elsewhere on the board
/12V DC Common Bank/12V DC Block 4/OUT_C2: J203.14; also elsewhere on the board
/12V DC Common Bank/12V DC Block 4/OUT_C3: J203.15; also elsewhere on the board
/12V DC Common Bank/12V DC Block 4/OUT_C4: J203.16; also elsewhere on the board
GND: C201.2, C202.2, C203.2, C204.2, JP202.1 (A), JP203.1 (A), JP204.1 (A), JP206.1 (A), JP207.1 (A), JP208.3 (B), U201.10 (VSS), U202.10 (VSS); also elsewhere on the board
unnamed: D201.1 (KA), R201.1
unnamed: D201.2 (AK), JP209.2
unnamed: J201.1, U201.19 (INTB)
unnamed: J202.1, U201.20 (INTA)
unnamed: J204.1, U202.19 (INTB)
unnamed: J205.1, U202.20 (INTA)
unnamed: J206.2_1 (02P), J206.2_2 (02P), J206.2_3 (02P), JP209.1, Q201.1 (G), Q202.1 (G), Q203.1 (G)
unnamed: JP201.1, U201.18 (~RESET~)
unnamed: JP202.2 (C), U201.17 (A2)
unnamed: JP203.2 (C), U201.16 (A1)
unnamed: JP204.2 (C), U201.15 (A0)
unnamed: JP205.1, U202.18 (~RESET~)
unnamed: JP206.2 (C), U202.17 (A2)
unnamed: JP207.2 (C), U202.16 (A1)
unnamed: JP208.2 (C), U202.15 (A0)
SCK: U201.12 (SCK), U202.12 (SCK); also elsewhere on the board
SDA: U201.13 (SDA), U202.13 (SDA); also elsewhere on the board

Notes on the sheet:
I2C Address 0x20
I2C Address 0x21
Reverse Polarity (Voltage) Protection Optional, can be substituded with shunt(s) or partially populated, see note above.
Note that reverse power protection does come with a slight power loss (3.1 mOhm per FET). For absolute best efficiency the FETs can be replaced with shunts disabling the protection. The power loss can be calculated using: (I / n ) ² * R * 0.0031 * n Current divided by number of FETs squared multipl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

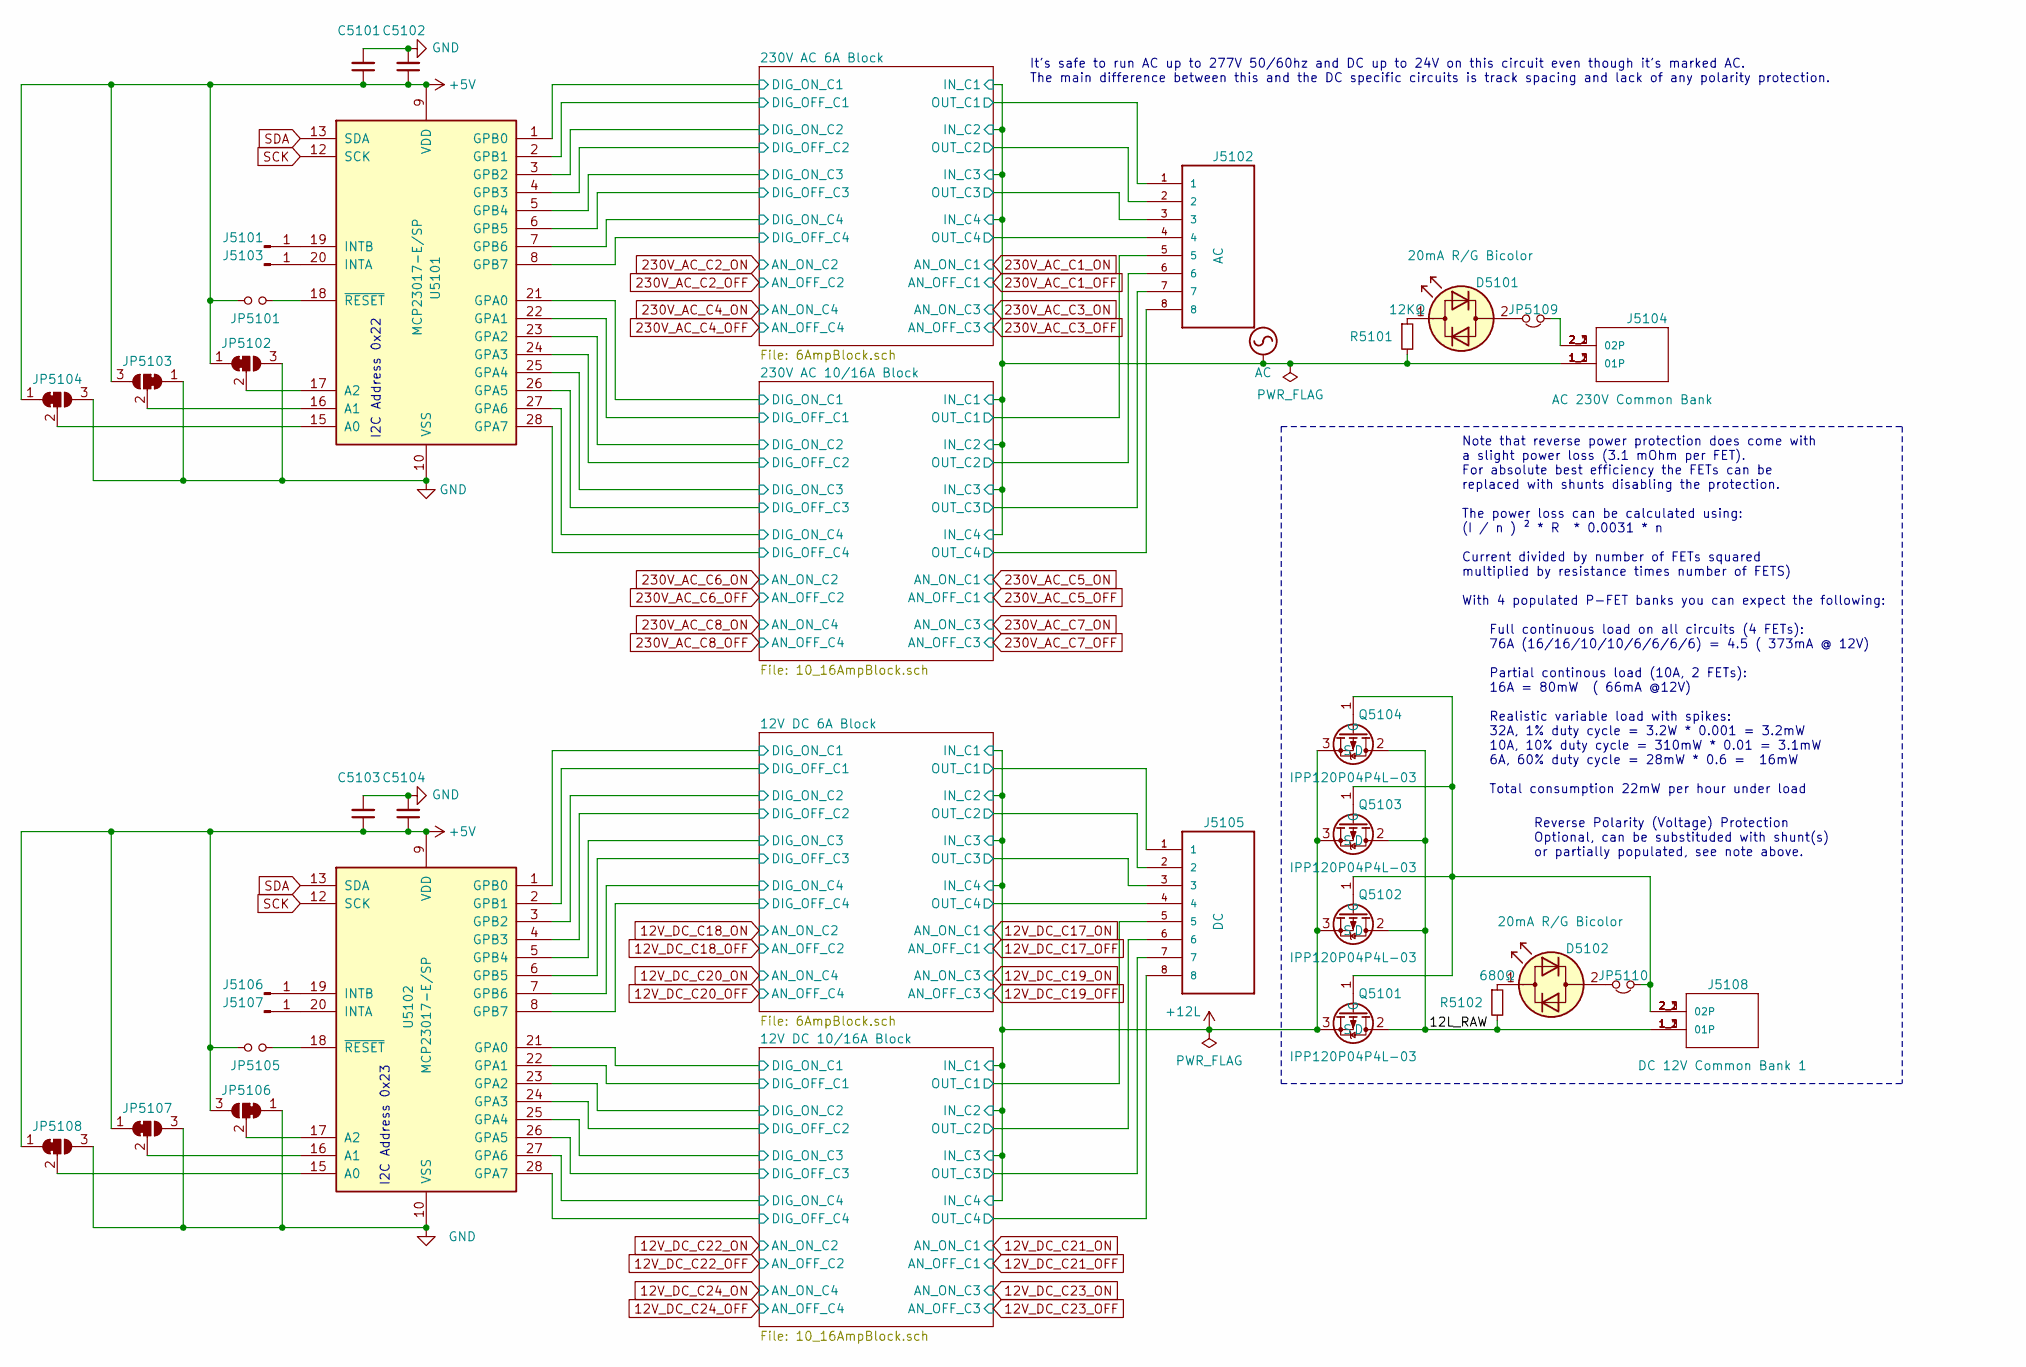
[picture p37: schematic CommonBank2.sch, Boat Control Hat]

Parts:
C5101, C5103: 10μF; C_Disc_D7.5mm_W5.0mm_P5.00mm
C5102, C5104: 0.1μF; C_Disc_D7.5mm_W5.0mm_P5.00mm
D5101, D5102: 20mA R/G Bicolor; LED_D5.0mm
J5101, J5103, J5106, J5107: Conn_01x01_Male; PinHeader_1x01_P2.54mm_Vertical
J5102, J5105: TBP01R2W-508-08BE; CUI_TBP01R2W-508-08BE
J5104, J5108: TBL008V-1000-02BE; CUI_TBL008V-1000-02BE
JP5101, JP5105: Jumper_NO_Small; PinHeader_1x02_P2.54mm_Vertical
JP5102, JP5103, JP5104, JP5106, JP5107, JP5108: SolderJumper_3_Bridged12; SolderJumper-3_P1.3mm_Bridged12_RoundedPad1.0x1.5mm
JP5109, JP5110: Jumper_NC_Small; PinHeader_1x02_P2.54mm_Vertical
Q5101, Q5102, Q5103, Q5104: IPP120P04P4L-03; TO-220-3_Vertical
R5101: 12KΩ; R_Axial_DIN0207_L6.3mm_D2.5mm_P7.62mm_Horizontal
R5102: 680Ω; R_Axial_DIN0207_L6.3mm_D2.5mm_P7.62mm_Horizontal
U5101, U5102: MCP23017-E/SP; DIP-28_W7.62mm

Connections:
+5V: C5101.1, C5102.1, C5103.1, C5104.1, JP5101.2, JP5102.1 (A), JP5103.3 (B), JP5104.1 (A), JP5105.2, JP5106.3 (B), JP5107.1 (A), JP5108.1 (A), U5101.9 (VDD), U5102.9 (VDD); also elsewhere on the board
+12L: Q5101.3 (S), Q5102.3 (S), Q5103.3 (S), Q5104.3 (S); also elsewhere on the board
/Mixed 12V DC / 230V AC Common Bank/12L_RAW: J5108.1_1 (01P), J5108.1_2 (01P), J5108.1_3 (01P), Q5101.2 (D), Q5102.2 (D), Q5103.2 (D), Q5104.2 (D), R5102.2
/Mixed 12V DC / 230V AC Common Bank/12V DC 6A Block/DIG_OFF_C1: U5102.2 (GPB1); also elsewhere on the board
/Mixed 12V DC / 230V AC Common Bank/12V DC 6A Block/DIG_OFF_C2: U5102.4 (GPB3); also elsewhere on the board
/Mixed 12V DC / 230V AC Common Bank/12V DC 6A Block/DIG_OFF_C3: U5102.6 (GPB5); also elsewhere on the board
/Mixed 12V DC / 230V AC Common Bank/12V DC 6A Block/DIG_OFF_C4: U5102.8 (GPB7); also elsewhere on the board
/Mixed 12V DC / 230V AC Common Bank/12V DC 6A Block/DIG_ON_C1: U5102.1 (GPB0); also elsewhere on the board
/Mixed 12V DC / 230V AC Common Bank/12V DC 6A Block/DIG_ON_C2: U5102.3 (GPB2); also elsewhere on the board
/Mixed 12V DC / 230V AC Common Bank/12V DC 6A Block/DIG_ON_C3: U5102.5 (GPB4); also elsewhere on the board
/Mixed 12V DC / 230V AC Common Bank/12V DC 6A Block/DIG_ON_C4: U5102.7 (GPB6); also elsewhere on the board
/Mixed 12V DC / 230V AC Common Bank/12V DC 6A Block/OUT_C1: J5105.1; also elsewhere on the board
/Mixed 12V DC / 230V AC Common Bank/12V DC 6A Block/OUT_C2: J5105.2; also elsewhere on the board
/Mixed 12V DC / 230V AC Common Bank/12V DC 6A Block/OUT_C3: J5105.3; also elsewhere on the board
/Mixed 12V DC / 230V AC Common Bank/12V DC 6A Block/OUT_C4: J5105.4; also elsewhere on the board
/Mixed 12V DC / 230V AC Common Bank/12V DC 10/16A Block/DIG_OFF_C1: U5102.22 (GPA1); also elsewhere on the board
/Mixed 12V DC / 230V AC Common Bank/12V DC 10/16A Block/DIG_OFF_C2: U5102.24 (GPA3); also elsewhere on the board
/Mixed 12V DC / 230V AC Common Bank/12V DC 10/16A Block/DIG_OFF_C3: U5102.26 (GPA5); also elsewhere on the board
/Mixed 12V DC / 230V AC Common Bank/12V DC 10/16A Block/DIG_OFF_C4: U5102.28 (GPA7); also elsewhere on the board
/Mixed 12V DC / 230V AC Common Bank/12V DC 10/16A Block/DIG_ON_C1: U5102.21 (GPA0); also elsewhere on the board
/Mixed 12V DC / 230V AC Common Bank/12V DC 10/16A Block/DIG_ON_C2: U5102.23 (GPA2); also elsewhere on the board
/Mixed 12V DC / 230V AC Common Bank/12V DC 10/16A Block/DIG_ON_C3: U5102.25 (GPA4); also elsewhere on the board
/Mixed 12V DC / 230V AC Common Bank/12V DC 10/16A Block/DIG_ON_C4: U5102.27 (GPA6); also elsewhere on the board
/Mixed 12V DC / 230V AC Common Bank/12V DC 10/16A Block/OUT_C1: J5105.5; also elsewhere on the board
/Mixed 12V DC / 230V AC Common Bank/12V DC 10/16A Block/OUT_C2: J5105.6; also elsewhere on the board
/Mixed 12V DC / 230V AC Common Bank/12V DC 10/16A Block/OUT_C3: J5105.7; also elsewhere on the board
/Mixed 12V DC / 230V AC Common Bank/12V DC 10/16A Block/OUT_C4: J5105.8; also elsewhere on the board
/Mixed 12V DC / 230V AC Common Bank/230V AC 6A Block/DIG_OFF_C1: U5101.2 (GPB1); also elsewhere on the board
/Mixed 12V DC / 230V AC Common Bank/230V AC 6A Block/DIG_OFF_C2: U5101.4 (GPB3); also elsewhere on the board
/Mixed 12V DC / 230V AC Common Bank/230V AC 6A Block/DIG_OFF_C3: U5101.6 (GPB5); also elsewhere on the board
/Mixed 12V DC / 230V AC Common Bank/230V AC 6A Block/DIG_OFF_C4: U5101.8 (GPB7); also elsewhere on the board
/Mixed 12V DC / 230V AC Common Bank/230V AC 6A Block/DIG_ON_C1: U5101.1 (GPB0); also elsewhere on the board
/Mixed 12V DC / 230V AC Common Bank/230V AC 6A Block/DIG_ON_C2: U5101.3 (GPB2); also elsewhere on the board
/Mixed 12V DC / 230V AC Common Bank/230V AC 6A Block/DIG_ON_C3: U5101.5 (GPB4); also elsewhere on the board
/Mixed 12V DC / 230V AC Common Bank/230V AC 6A Block/DIG_ON_C4: U5101.7 (GPB6); also elsewhere on the board
/Mixed 12V DC / 230V AC Common Bank/230V AC 6A Block/OUT_C1: J5102.1; also elsewhere on the board
/Mixed 12V DC / 230V AC Common Bank/230V AC 6A Block/OUT_C2: J5102.2; also elsewhere on the board
/Mixed 12V DC / 230V AC Common Bank/230V AC 6A Block/OUT_C3: J5102.3; also elsewhere on the board
/Mixed 12V DC / 230V AC Common Bank/230V AC 6A Block/OUT_C4: J5102.4; also elsewhere on the board
/Mixed 12V DC / 230V AC Common Bank/230V AC 10/16A Block/DIG_OFF_C1: U5101.22 (GPA1); also elsewhere on the board
/Mixed 12V DC / 230V AC Common Bank/230V AC 10/16A Block/DIG_OFF_C2: U5101.24 (GPA3); also elsewhere on the board
/Mixed 12V DC / 230V AC Common Bank/230V AC 10/16A Block/DIG_OFF_C3: U5101.26 (GPA5); also elsewhere on the board
/Mixed 12V DC / 230V AC Common Bank/230V AC 10/16A Block/DIG_OFF_C4: U5101.28 (GPA7); also elsewhere on the board
/Mixed 12V DC / 230V AC Common Bank/230V AC 10/16A Block/DIG_ON_C1: U5101.21 (GPA0); also elsewhere on the board
/Mixed 12V DC / 230V AC Common Bank/230V AC 10/16A Block/DIG_ON_C2: U5101.23 (GPA2); also elsewhere on the board
/Mixed 12V DC / 230V AC Common Bank/230V AC 10/16A Block/DIG_ON_C3: U5101.25 (GPA4); also elsewhere on the board
/Mixed 12V DC / 230V AC Common Bank/230V AC 10/16A Block/DIG_ON_C4: U5101.27 (GPA6); also elsewhere on the board
/Mixed 12V DC / 230V AC Common Bank/230V AC 10/16A Block/OUT_C1: J5102.5; also elsewhere on the board
/Mixed 12V DC / 230V AC Common Bank/230V AC 10/16A Block/OUT_C2: J5102.6; also elsewhere on the board
/Mixed 12V DC / 230V AC Common Bank/230V AC 10/16A Block/OUT_C3: J5102.7; also elsewhere on the board
/Mixed 12V DC / 230V AC Common Bank/230V AC 10/16A Block/OUT_C4: J5102.8; also elsewhere on the board
AC: J5104.1_1 (01P), J5104.1_2 (01P), J5104.1_3 (01P), R5101.2; also elsewhere on the board
GND: C5101.2, C5102.2, C5103.2, C5104.2, JP5102.3 (B), JP5103.1 (A), JP5104.3 (B), JP5106.1 (A), JP5107.3 (B), JP5108.3 (B), U5101.10 (VSS), U5102.10 (VSS); also elsewhere on the board
unnamed: D5101.1 (KA), R5101.1
unnamed: D5101.2 (AK), JP5109.2
unnamed: D5102.1 (KA), R5102.1
unnamed: D5102.2 (AK), JP5110.2
unnamed: J5101.1, U5101.19 (INTB)
unnamed: J5103.1, U5101.20 (INTA)
unnamed: J5104.2_1 (02P), J5104.2_2 (02P), J5104.2_3 (02P), JP5109.1
unnamed: J5106.1, U5102.19 (INTB)
unnamed: J5107.1, U5102.20 (INTA)
unnamed: J5108.2_1 (02P), J5108.2_2 (02P), J5108.2_3 (02P), JP5110.1, Q5101.1 (G), Q5102.1 (G), Q5103.1 (G), Q5104.1 (G)
unnamed: JP5101.1, U5101.18 (~RESET~)
unnamed: JP5102.2 (C), U5101.17 (A2)
unnamed: JP5103.2 (C), U5101.16 (A1)
unnamed: JP5104.2 (C), U5101.15 (A0)
unnamed: JP5105.1, U5102.18 (~RESET~)
unnamed: JP5106.2 (C), U5102.17 (A2)
unnamed: JP5107.2 (C), U5102.16 (A1)
unnamed: JP5108.2 (C), U5102.15 (A0)
SCK: U5101.12 (SCK), U5102.12 (SCK); also elsewhere on the board
SDA: U5101.13 (SDA), U5102.13 (SDA); also elsewhere on the board

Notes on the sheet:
I2C Address 0x23
I2C Address 0x22
It's safe to run AC up to 277V 50/60hz and DC up to 24V on this circuit even though it's marked AC. The main difference between this and the DC specific circuits is track spacing and lack of any polarity protection.
Reverse Polarity (Voltage) Protection Optional, can be substituded with shunt(s) or partially populated, see note above.
Note that reverse power protection does come with a slight power loss (3.1 mOhm per FET). For absolute best efficiency the FETs can be replaced with shunts disabling the protection. The power loss can be calculated using: (I / n ) ² * R * 0.0031 * n Current divided by number of FETs squared multipl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

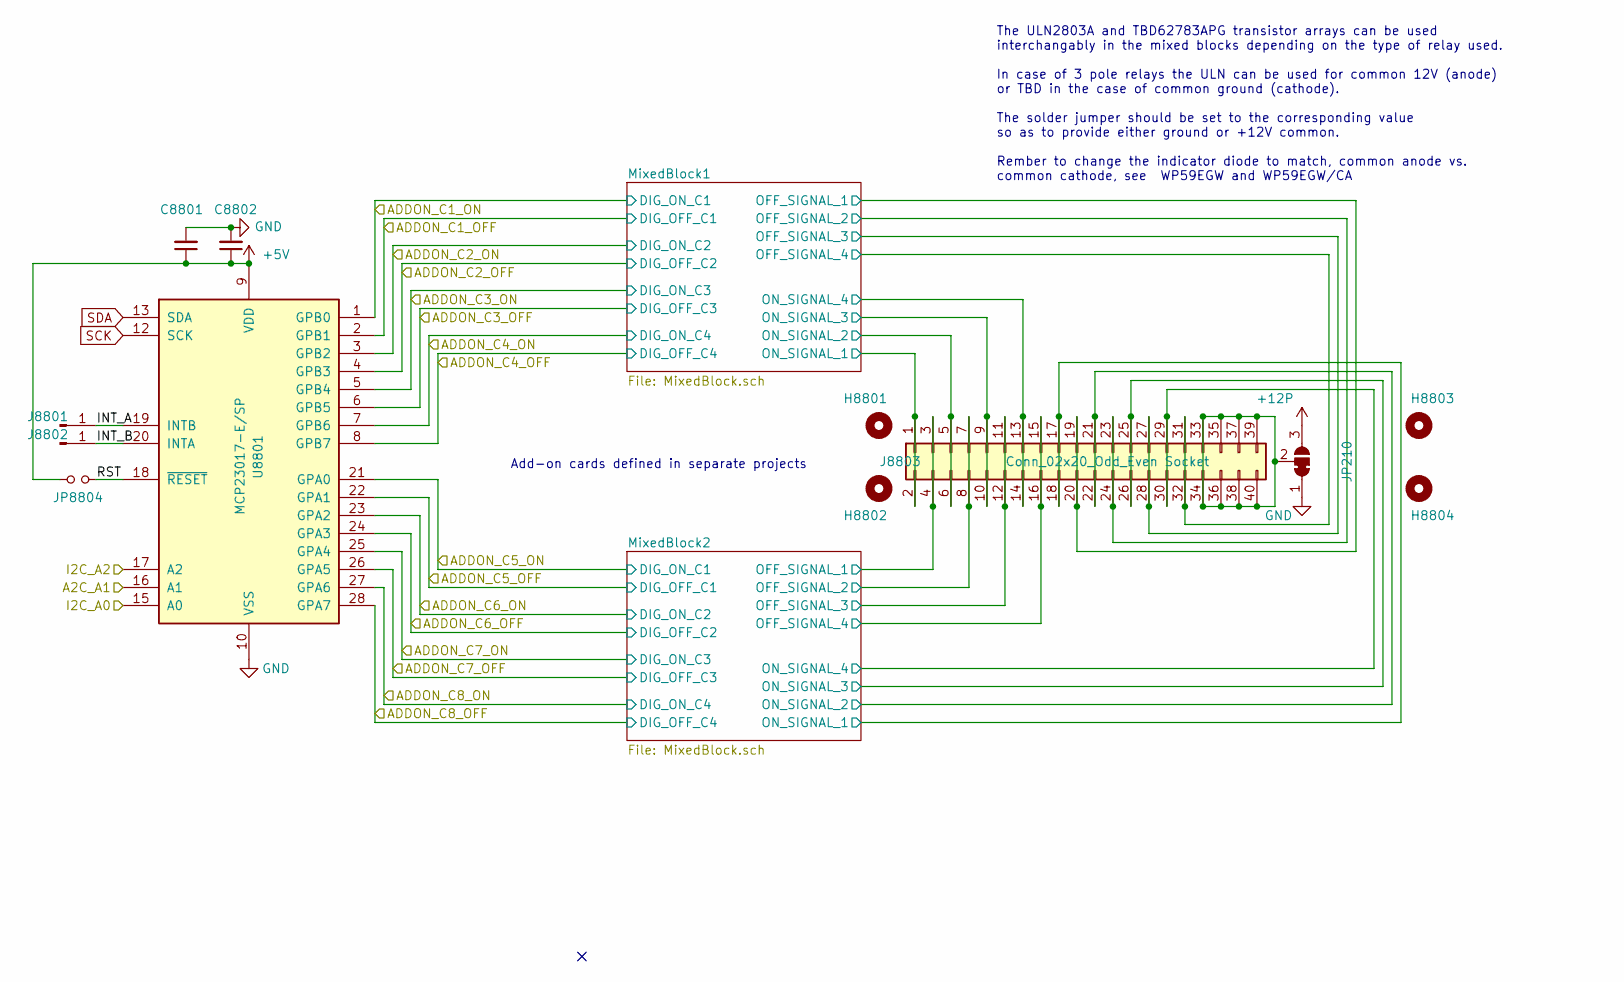
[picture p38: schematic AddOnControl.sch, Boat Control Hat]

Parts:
C8801: 10uF; C_Disc_D7.5mm_W5.0mm_P5.00mm
C8802: 0.1uF; C_Disc_D7.5mm_W5.0mm_P5.00mm
H3901, H3902, H3903, H3904: MountingHole; MountingHole_3mm
J3901, J3902: Conn_01x01_Male; PinHeader_1x01_P2.54mm_Vertical
J3903: Conn_02x20_Odd_Even Socket; PinHeader_2x20_P2.54mm_Vertical
JP210: SolderJumper_3_Bridged12; SolderJumper-3_P1.3mm_Open_RoundedPad3.0x4.5mm_NumberLabels
JP3901: Jumper_NO_Small; PinHeader_1x02_P2.54mm_Vertical
U3901: MCP23017-E/SP; DIP-28_W7.62mm

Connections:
+5V: C8801.1, C8802.1, JP3901.2, U3901.9 (VDD); also elsewhere on the board
+12P: JP210.3 (B); also elsewhere on the board
/Add-On Relay Board 1/A2C_A1: U3901.16 (A1); also elsewhere on the board
/Add-On Relay Board 1/ADDON_C1_OFF: U3901.2 (GPB1); also elsewhere on the board
/Add-On Relay Board 1/ADDON_C1_ON: U3901.1 (GPB0); also elsewhere on the board
/Add-On Relay Board 1/ADDON_C2_OFF: U3901.4 (GPB3); also elsewhere on the board
/Add-On Relay Board 1/ADDON_C2_ON: U3901.3 (GPB2); also elsewhere on the board
/Add-On Relay Board 1/ADDON_C3_OFF: U3901.6 (GPB5); also elsewhere on the board
/Add-On Relay Board 1/ADDON_C3_ON: U3901.5 (GPB4); also elsewhere on the board
/Add-On Relay Board 1/ADDON_C4_OFF: U3901.8 (GPB7); also elsewhere on the board
/Add-On Relay Board 1/ADDON_C4_ON: U3901.7 (GPB6); also elsewhere on the board
/Add-On Relay Board 1/ADDON_C5_OFF: U3901.22 (GPA1); also elsewhere on the board
/Add-On Relay Board 1/ADDON_C5_ON: U3901.21 (GPA0); also elsewhere on the board
/Add-On Relay Board 1/ADDON_C6_OFF: U3901.24 (GPA3); also elsewhere on the board
/Add-On Relay Board 1/ADDON_C6_ON: U3901.23 (GPA2); also elsewhere on the board
/Add-On Relay Board 1/ADDON_C7_OFF: U3901.26 (GPA5); also elsewhere on the board
/Add-On Relay Board 1/ADDON_C7_ON: U3901.25 (GPA4); also elsewhere on the board
/Add-On Relay Board 1/ADDON_C8_OFF: U3901.28 (GPA7); also elsewhere on the board
/Add-On Relay Board 1/ADDON_C8_ON: U3901.27 (GPA6); also elsewhere on the board
/Add-On Relay Board 1/I2C_A0: U3901.15 (A0); also elsewhere on the board
/Add-On Relay Board 1/I2C_A2: U3901.17 (A2); also elsewhere on the board
/Add-On Relay Board 1/INT_A: J3901.1, U3901.19 (INTB)
/Add-On Relay Board 1/INT_B: J3902.1, U3901.20 (INTA)
/Add-On Relay Board 1/MixedBlock1/OFF_SIGNAL_1: J3903.19, J3903.20; also elsewhere on the board
/Add-On Relay Board 1/MixedBlock1/OFF_SIGNAL_2: J3903.23, J3903.24; also elsewhere on the board
/Add-On Relay Board 1/MixedBlock1/OFF_SIGNAL_3: J3903.27, J3903.28; also elsewhere on the board
/Add-On Relay Board 1/MixedBlock1/OFF_SIGNAL_4: J3903.31, J3903.32; also elsewhere on the board
/Add-On Relay Board 1/MixedBlock1/ON_SIGNAL_1: J3903.1, J3903.2; also elsewhere on the board
/Add-On Relay Board 1/MixedBlock1/ON_SIGNAL_2: J3903.5, J3903.6; also elsewhere on the board
/Add-On Relay Board 1/MixedBlock1/ON_SIGNAL_3: J3903.9, J3903.10; also elsewhere on the board
/Add-On Relay Board 1/MixedBlock1/ON_SIGNAL_4: J3903.13, J3903.14; also elsewhere on the board
/Add-On Relay Board 1/MixedBlock2/OFF_SIGNAL_1: J3903.3, J3903.4; also elsewhere on the board
/Add-On Relay Board 1/MixedBlock2/OFF_SIGNAL_2: J3903.7, J3903.8; also elsewhere on the board
/Add-On Relay Board 1/MixedBlock2/OFF_SIGNAL_3: J3903.11, J3903.12; also elsewhere on the board
/Add-On Relay Board 1/MixedBlock2/OFF_SIGNAL_4: J3903.15, J3903.16; also elsewhere on the board
/Add-On Relay Board 1/MixedBlock2/ON_SIGNAL_1: J3903.17, J3903.18; also elsewhere on the board
/Add-On Relay Board 1/MixedBlock2/ON_SIGNAL_2: J3903.21, J3903.22; also elsewhere on the board
/Add-On Relay Board 1/MixedBlock2/ON_SIGNAL_3: J3903.25, J3903.26; also elsewhere on the board
/Add-On Relay Board 1/MixedBlock2/ON_SIGNAL_4: J3903.29, J3903.30; also elsewhere on the board
/Add-On Relay Board 1/RST: JP3901.1, U3901.18 (~RESET~)
GND: C8801.2, C8802.2, JP210.1 (A), U3901.10 (VSS); also elsewhere on the board
SCK: U3901.12 (SCK); also elsewhere on the board
SDA: U3901.13 (SDA); also elsewhere on the board

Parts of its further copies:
C3901: 10uF; C_Disc_D7.5mm_W5.0mm_P5.00mm
C3902: 0.1uF; C_Disc_D7.5mm_W5.0mm_P5.00mm
H8801, H8802, H8803, H8804: MountingHole; MountingHole_3mm
J8801, J8802: Conn_01x01_Male; PinHeader_1x01_P2.54mm_Vertical
J8803: Conn_02x20_Odd_Even Socket; PinHeader_2x20_P2.54mm_Vertical
JP8701: SolderJumper_3_Bridged12; SolderJumper-3_P1.3mm_Open_RoundedPad3.0x4.5mm_NumberLabels
JP8804: Jumper_NO_Small; PinHeader_1x02_P2.54mm_Vertical
U8801: MCP23017-E/SP; DIP-28_W7.62mm

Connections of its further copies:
+5V: C3901.1, C3902.1, JP8804.2, U8801.9 (VDD); also elsewhere on the board
+12P: JP8701.3 (B); also elsewhere on the board
/Add-On Relay Board 2/A2C_A1: U8801.16 (A1); also elsewhere on the board
/Add-On Relay Board 2/ADDON_C1_OFF: U8801.2 (GPB1); also elsewhere on the board
/Add-On Relay Board 2/ADDON_C1_ON: U8801.1 (GPB0); also elsewhere on the board
/Add-On Relay Board 2/ADDON_C2_OFF: U8801.4 (GPB3); also elsewhere on the board
/Add-On Relay Board 2/ADDON_C2_ON: U8801.3 (GPB2); also elsewhere on the board
/Add-On Relay Board 2/ADDON_C3_OFF: U8801.6 (GPB5); also elsewhere on the board
/Add-On Relay Board 2/ADDON_C3_ON: U8801.5 (GPB4); also elsewhere on the board
/Add-On Relay Board 2/ADDON_C4_OFF: U8801.8 (GPB7); also elsewhere on the board
/Add-On Relay Board 2/ADDON_C4_ON: U8801.7 (GPB6); also elsewhere on the board
/Add-On Relay Board 2/ADDON_C5_OFF: U8801.22 (GPA1); also elsewhere on the board
/Add-On Relay Board 2/ADDON_C5_ON: U8801.21 (GPA0); also elsewhere on the board
/Add-On Relay Board 2/ADDON_C6_OFF: U8801.24 (GPA3); also elsewhere on the board
/Add-On Relay Board 2/ADDON_C6_ON: U8801.23 (GPA2); also elsewhere on the board
/Add-On Relay Board 2/ADDON_C7_OFF: U8801.26 (GPA5); also elsewhere on the board
/Add-On Relay Board 2/ADDON_C7_ON: U8801.25 (GPA4); also elsewhere on the board
/Add-On Relay Board 2/ADDON_C8_OFF: U8801.28 (GPA7); also elsewhere on the board
/Add-On Relay Board 2/ADDON_C8_ON: U8801.27 (GPA6); also elsewhere on the board
/Add-On Relay Board 2/I2C_A0: U8801.15 (A0); also elsewhere on the board
/Add-On Relay Board 2/I2C_A2: U8801.17 (A2); also elsewhere on the board
/Add-On Relay Board 2/INT_A: J8801.1, U8801.19 (INTB)
/Add-On Relay Board 2/INT_B: J8802.1, U8801.20 (INTA)
/Add-On Relay Board 2/MixedBlock1/OFF_SIGNAL_1: J8803.19, J8803.20; also elsewhere on the board
/Add-On Relay Board 2/MixedBlock1/OFF_SIGNAL_2: J8803.23, J8803.24; also elsewhere on the board
/Add-On Relay Board 2/MixedBlock1/OFF_SIGNAL_3: J8803.27, J8803.28; also elsewhere on the board
/Add-On Relay Board 2/MixedBlock1/OFF_SIGNAL_4: J8803.31, J8803.32; also elsewhere on the board
/Add-On Relay Board 2/MixedBlock1/ON_SIGNAL_1: J8803.1, J8803.2; also elsewhere on the board
/Add-On Relay Board 2/MixedBlock1/ON_SIGNAL_2: J8803.5, J8803.6; also elsewhere on the board
/Add-On Relay Board 2/MixedBlock1/ON_SIGNAL_3: J8803.9, J8803.10; also elsewhere on the board
/Add-On Relay Board 2/MixedBlock1/ON_SIGNAL_4: J8803.13, J8803.14; also elsewhere on the board
/Add-On Relay Board 2/MixedBlock2/OFF_SIGNAL_1: J8803.3, J8803.4; also elsewhere on the board
/Add-On Relay Board 2/MixedBlock2/OFF_SIGNAL_2: J8803.7, J8803.8; also elsewhere on the board
/Add-On Relay Board 2/MixedBlock2/OFF_SIGNAL_3: J8803.11, J8803.12; also elsewhere on the board
/Add-On Relay Board 2/MixedBlock2/OFF_SIGNAL_4: J8803.15, J8803.16; also elsewhere on the board
/Add-On Relay Board 2/MixedBlock2/ON_SIGNAL_1: J8803.17, J8803.18; also elsewhere on the board
/Add-On Relay Board 2/MixedBlock2/ON_SIGNAL_2: J8803.21, J8803.22; also elsewhere on the board
/Add-On Relay Board 2/MixedBlock2/ON_SIGNAL_3: J8803.25, J8803.26; also elsewhere on the board
/Add-On Relay Board 2/MixedBlock2/ON_SIGNAL_4: J8803.29, J8803.30; also elsewhere on the board
/Add-On Relay Board 2/RST: JP8804.1, U8801.18 (~RESET~)
GND: C3901.2, C3902.2, JP8701.1 (A), U8801.10 (VSS); also elsewhere on the board
SCK: U8801.12 (SCK); also elsewhere on the board
SDA: U8801.13 (SDA); also elsewhere on the board

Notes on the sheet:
Add-on cards defined in separate projects
The ULN2803A and TBD62783APG transistor arrays can be used interchangably in the mixed blocks depending on the type of relay used. In case of 3 pole relays the ULN can be used for common 12V (anode) or TBD in the case of common ground (cathode). The solder jumper should be set to the corresponding 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

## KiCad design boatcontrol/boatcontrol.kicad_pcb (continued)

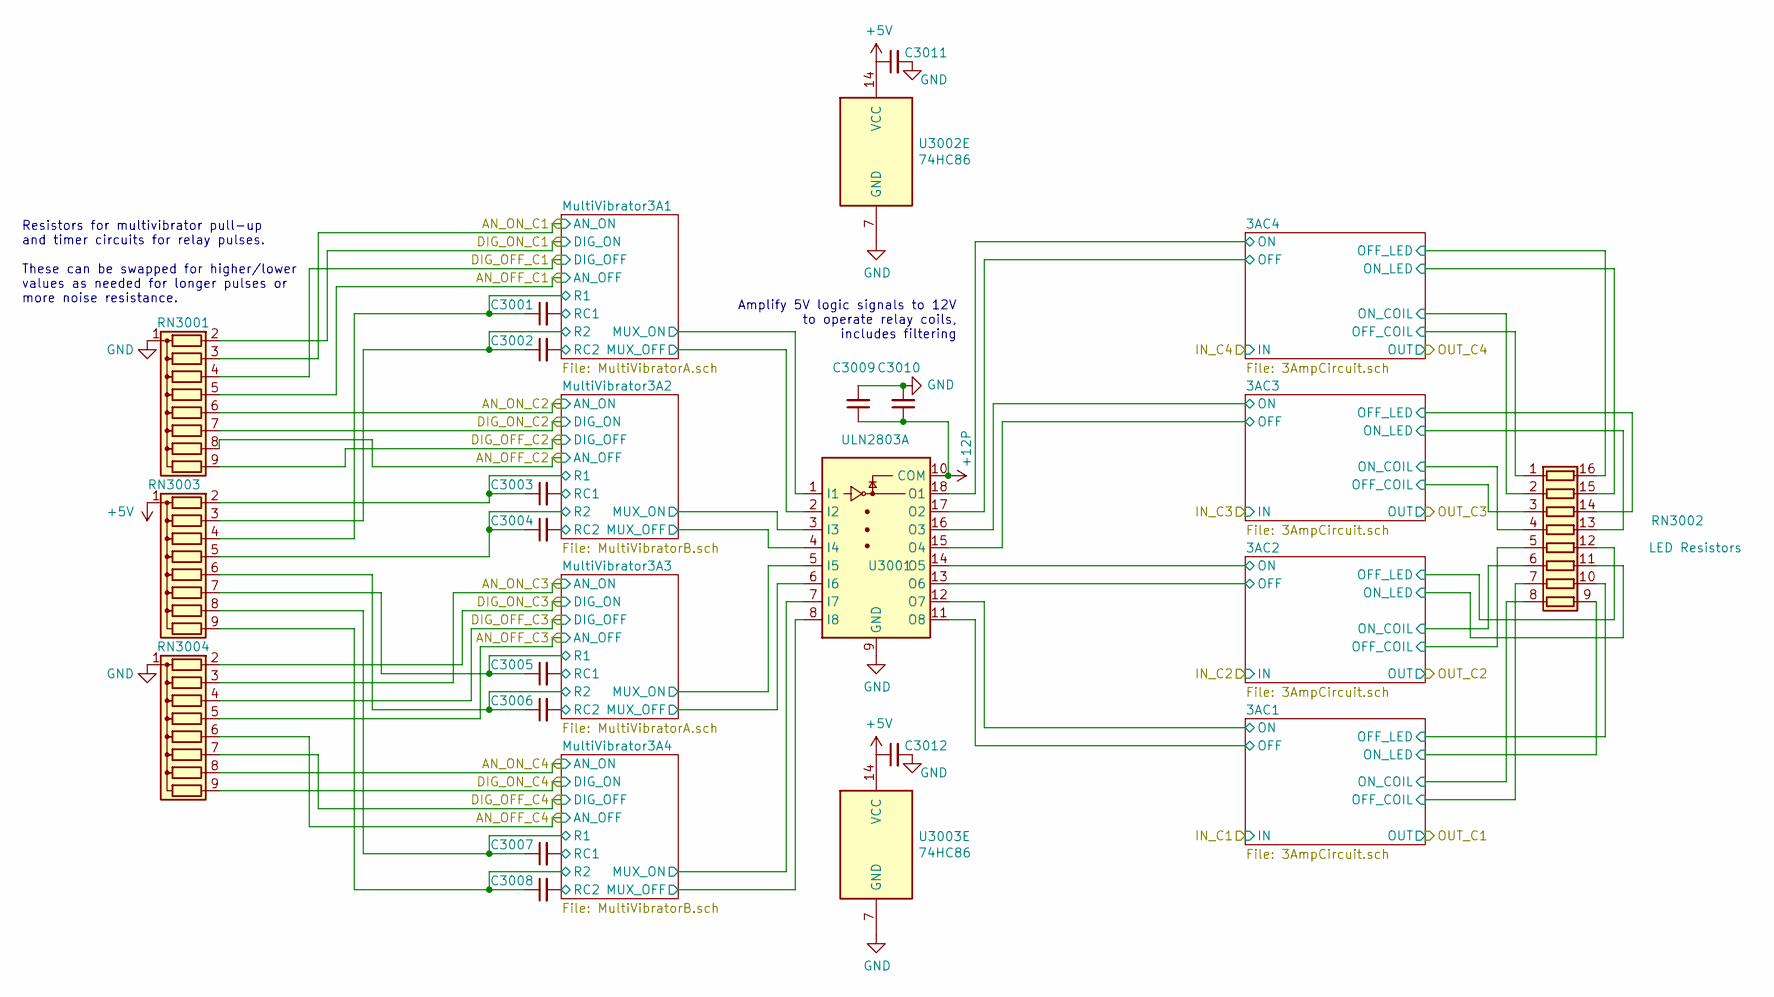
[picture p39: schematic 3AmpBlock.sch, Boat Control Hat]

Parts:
C1209: 10uF; C_Disc_D7.5mm_W5.0mm_P5.00mm
C1210, C1211, C1212: 0.1uF; C_Disc_D7.5mm_W5.0mm_P5.00mm
C3001, C3003, C3004, C3005, C3006, C3007, C3008: 1µF; C_Disc_D7.5mm_W5.0mm_P5.00mm
C3002: 1uF; C_Disc_D7.5mm_W5.0mm_P5.00mm
RN301, RN304: 100KΩ; R_Array_SIP9; Manufacturer_Part_Number 4609X-101-105LF
RN3002: 680Ω; DIP254P762X432-16P
RN3003: 10MΩ; R_Array_SIP9
U302, U303: 74HC86; DIP-14_W7.62mm
U3001: ULN2803A; DIP-18_W7.62mm

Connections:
12V_DC_C3_OFF: RN304.5 (R4); also elsewhere on the board
12V_DC_C3_ON: RN304.3 (R2); also elsewhere on the board
12V_DC_C4_OFF: RN304.6 (R5); also elsewhere on the board
12V_DC_C4_ON: RN304.8 (R7); also elsewhere on the board
+5V: C1211.1, C1212.1, RN3003.1 (common), U302.14 (VCC), U303.14 (VCC); also elsewhere on the board
+12P: C1209.1, C1210.1, U3001.10 (COM); also elsewhere on the board
/12V DC Common Bank/12V DC Block 1/DIG_OFF_C1: RN301.4 (R3); also elsewhere on the board
/12V DC Common Bank/12V DC Block 1/DIG_OFF_C2: RN301.9 (R8); also elsewhere on the board
/12V DC Common Bank/12V DC Block 1/DIG_OFF_C3: RN304.4 (R3); also elsewhere on the board
/12V DC Common Bank/12V DC Block 1/DIG_OFF_C4: RN304.7 (R6); also elsewhere on the board
/12V DC Common Bank/12V DC Block 1/DIG_ON_C1: RN301.2 (R1); also elsewhere on the board
/12V DC Common Bank/12V DC Block 1/DIG_ON_C2: RN301.7 (R6); also elsewhere on the board
/12V DC Common Bank/12V DC Block 1/DIG_ON_C3: RN304.2 (R1); also elsewhere on the board
/12V DC Common Bank/12V DC Block 1/DIG_ON_C4: RN304.9 (R8); also elsewhere on the board
/12V DC Common Bank/12V DC Block 4/3AC1/OFF: U3001.11 (O8); also elsewhere on the board
/12V DC Common Bank/12V DC Block 4/3AC1/OFF_COIL: RN3002.7 (R7.1); also elsewhere on the board
/12V DC Common Bank/12V DC Block 4/3AC1/OFF_LED: RN3002.10 (R7.2); also elsewhere on the board
/12V DC Common Bank/12V DC Block 4/3AC1/ON: U3001.12 (O7); also elsewhere on the board
/12V DC Common Bank/12V DC Block 4/3AC1/ON_COIL: RN3002.8 (R8.1); also elsewhere on the board
/12V DC Common Bank/12V DC Block 4/3AC1/ON_LED: RN3002.9 (R8.2); also elsewhere on the board
/12V DC Common Bank/12V DC Block 4/3AC2/OFF: U3001.13 (O6); also elsewhere on the board
/12V DC Common Bank/12V DC Block 4/3AC2/OFF_COIL: RN3002.5 (R5.1); also elsewhere on the board
/12V DC Common Bank/12V DC Block 4/3AC2/OFF_LED: RN3002.12 (R5.2); also elsewhere on the board
/12V DC Common Bank/12V DC Block 4/3AC2/ON: U3001.14 (O5); also elsewhere on the board
/12V DC Common Bank/12V DC Block 4/3AC2/ON_COIL: RN3002.6 (R6.1); also elsewhere on the board
/12V DC Common Bank/12V DC Block 4/3AC2/ON_LED: RN3002.11 (R6.2); also elsewhere on the board
/12V DC Common Bank/12V DC Block 4/3AC3/OFF: U3001.15 (O4); also elsewhere on the board
/12V DC Common Bank/12V DC Block 4/3AC3/OFF_COIL: RN3002.3 (R3.1); also elsewhere on the board
/12V DC Common Bank/12V DC Block 4/3AC3/OFF_LED: RN3002.14 (R3.2); also elsewhere on the board
/12V DC Common Bank/12V DC Block 4/3AC3/ON: U3001.16 (O3); also elsewhere on the board
/12V DC Common Bank/12V DC Block 4/3AC3/ON_COIL: RN3002.4 (R4.1); also elsewhere on the board
/12V DC Common Bank/12V DC Block 4/3AC3/ON_LED: RN3002.13 (R4.2); also elsewhere on the board
/12V DC Common Bank/12V DC Block 4/3AC4/OFF: U3001.17 (O2); also elsewhere on the board
/12V DC Common Bank/12V DC Block 4/3AC4/OFF_COIL: RN3002.1 (R1.1); also elsewhere on the board
/12V DC Common Bank/12V DC Block 4/3AC4/OFF_LED: RN3002.16 (R1.2); also elsewhere on the board
/12V DC Common Bank/12V DC Block 4/3AC4/ON: U3001.18 (O1); also elsewhere on the board
/12V DC Common Bank/12V DC Block 4/3AC4/ON_COIL: RN3002.2 (R2.1); also elsewhere on the board
/12V DC Common Bank/12V DC Block 4/3AC4/ON_LED: RN3002.15 (R2.2); also elsewhere on the board
/12V DC Common Bank/12V DC Block 4/MultiVibrator3A1/MUX_OFF: U3001.2 (I2); also elsewhere on the board
/12V DC Common Bank/12V DC Block 4/MultiVibrator3A1/MUX_ON: U3001.1 (I1); also elsewhere on the board
/12V DC Common Bank/12V DC Block 4/MultiVibrator3A1/R1: C3001.1, RN3003.4 (R3); also elsewhere on the board
/12V DC Common Bank/12V DC Block 4/MultiVibrator3A1/R2: C3002.1, RN3003.3 (R2); also elsewhere on the board
/12V DC Common Bank/12V DC Block 4/MultiVibrator3A1/RC1: C3001.2; also elsewhere on the board
/12V DC Common Bank/12V DC Block 4/MultiVibrator3A1/RC2: C3002.2; also elsewhere on the board
/12V DC Common Bank/12V DC Block 4/MultiVibrator3A2/MUX_OFF: U3001.4 (I4); also elsewhere on the board
/12V DC Common Bank/12V DC Block 4/MultiVibrator3A2/MUX_ON: U3001.3 (I3); also elsewhere on the board
/12V DC Common Bank/12V DC Block 4/MultiVibrator3A2/R1: C3003.1, RN3003.2 (R1); also elsewhere on the board
/12V DC Common Bank/12V DC Block 4/MultiVibrator3A2/R2: C3004.1, RN3003.5 (R4); also elsewhere on the board
/12V DC Common Bank/12V DC Block 4/MultiVibrator3A2/RC1: C3003.2; also elsewhere on the board
/12V DC Common Bank/12V DC Block 4/MultiVibrator3A2/RC2: C3004.2; also elsewhere on the board
/12V DC Common Bank/12V DC Block 4/MultiVibrator3A3/MUX_OFF: U3001.6 (I6); also elsewhere on the board
/12V DC Common Bank/12V DC Block 4/MultiVibrator3A3/MUX_ON: U3001.5 (I5); also elsewhere on the board
/12V DC Common Bank/12V DC Block 4/MultiVibrator3A3/R1: C3005.1, RN3003.7 (R6); also elsewhere on the board
/12V DC Common Bank/12V DC Block 4/MultiVibrator3A3/R2: C3006.1, RN3003.6 (R5); also elsewhere on the board
/12V DC Common Bank/12V DC Block 4/MultiVibrator3A3/RC1: C3005.2; also elsewhere on the board
/12V DC Common Bank/12V DC Block 4/MultiVibrator3A3/RC2: C3006.2; also elsewhere on the board
/12V DC Common Bank/12V DC Block 4/MultiVibrator3A4/MUX_OFF: U3001.8 (I8); also elsewhere on the board
/12V DC Common Bank/12V DC Block 4/MultiVibrator3A4/MUX_ON: U3001.7 (I7); also elsewhere on the board
/12V DC Common Bank/12V DC Block 4/MultiVibrator3A4/R1: C3007.1, RN3003.8 (R7); also elsewhere on the board
/12V DC Common Bank/12V DC Block 4/MultiVibrator3A4/R2: C3008.1, RN3003.9 (R8); also elsewhere on the board
/12V DC Common Bank/12V DC Block 4/MultiVibrator3A4/RC1: C3007.2; also elsewhere on the board
/12V DC Common Bank/12V DC Block 4/MultiVibrator3A4/RC2: C3008.2; also elsewhere on the board
GND: C1209.2, C1210.2, C1211.2, C1212.2, RN301.1 (common), RN304.1 (common), U302.7 (GND), U303.7 (GND), U3001.9 (GND); also elsewhere on the board

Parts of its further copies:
C301, C303, C304, C305, C306, C307, C308, C1201, C1203, C1204, C1205, C1206, C1207, C1208, C2101, C2103, C2104, C2105, C2106, C2107, C2108: 1µF; C_Disc_D7.5mm_W5.0mm_P5.00mm
C302, C1202, C2102: 1uF; C_Disc_D7.5mm_W5.0mm_P5.00mm
C309, C2109, C3009: 10uF; C_Disc_D7.5mm_W5.0mm_P5.00mm
C310, C311, C312, C2110, C2111, C2112, C3010, C3011, C3012: 0.1uF; C_Disc_D7.5mm_W5.0mm_P5.00mm
RN302, RN1202, RN2102: 680Ω; DIP254P762X432-16P
RN303, RN1203, RN2103: 10MΩ; R_Array_SIP9
RN1201, RN1204, RN2101, RN2104, RN3001, RN3004: 100KΩ; R_Array_SIP9; Manufacturer_Part_Number 4609X-101-105LF
U301, U1201, U2101: ULN2803A; DIP-18_W7.62mm
U1202, U1203, U2102, U3002, U3003: 74HC86; DIP-14_W7.62mm

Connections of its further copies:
12V_DC_C5_OFF: RN1201.5 (R4), U1202.5; also elsewhere on the board
12V_DC_C5_ON: RN1201.3 (R2), U1202.2; also elsewhere on the board
12V_DC_C6_OFF: RN1201.8 (R7), U1202.13; also elsewhere on the board
12V_DC_C6_ON: RN1201.6 (R5), U1202.10; also elsewhere on the board
12V_DC_C7_OFF: RN1204.5 (R4), U1203.5; also elsewhere on the board
12V_DC_C7_ON: RN1204.3 (R2), U1203.2; also elsewhere on the board
12V_DC_C8_OFF: RN1204.6 (R5), U1203.13; also elsewhere on the board
12V_DC_C8_ON: RN1204.8 (R7), U1203.10; also elsewhere on the board
12V_DC_C9_OFF: RN2101.5 (R4), U2102.5; also elsewhere on the board
12V_DC_C9_ON: RN2101.3 (R2), U2102.2; also elsewhere on the board
12V_DC_C10_OFF: RN2101.8 (R7), U2102.13; also elsewhere on the board
12V_DC_C10_ON: RN2101.6 (R5), U2102.10; also elsewhere on the board
12V_DC_C13_OFF: RN3001.5 (R4), U3002.5; also elsewhere on the board
12V_DC_C13_ON: RN3001.3 (R2), U3002.2; also elsewhere on the board
12V_DC_C14_OFF: RN3001.8 (R7), U3002.13; also elsewhere on the board
12V_DC_C14_ON: RN3001.6 (R5), U3002.10; also elsewhere on the board
12V_DC_C15_OFF: RN3004.5 (R4), U3003.5; also elsewhere on the board
12V_DC_C15_ON: RN3004.3 (R2), U3003.2; also elsewhere on the board
12V_DC_C16_OFF: RN3004.6 (R5), U3003.13; also elsewhere on the board
12V_DC_C16_ON: RN3004.8 (R7), U3003.10; also elsewhere on the board
+5V: C311.1, C312.1, C2111.1, C2112.1, C3011.1, C3012.1, RN303.1 (common), RN1203.1 (common), RN2103.1 (common), U1202.14 (VCC), U1203.14 (VCC), U2102.14 (VCC), U3002.14 (VCC), U3003.14 (VCC); also elsewhere on the board
+12P: C309.1, C310.1, C2109.1, C2110.1, C3009.1, C3010.1, U301.10 (COM), U1201.10 (COM), U2101.10 (COM); also elsewhere on the board
/12V DC Common Bank/12V DC Block 1/3AC1/OFF: U301.11 (O8); also elsewhere on the board
/12V DC Common Bank/12V DC Block 1/3AC1/OFF_COIL: RN302.7 (R7.1); also elsewhere on the board
/12V DC Common Bank/12V DC Block 1/3AC1/OFF_LED: RN302.10 (R7.2); also elsewhere on the board
/12V DC Common Bank/12V DC Block 1/3AC1/ON: U301.12 (O7); also elsewhere on the board
/12V DC Common Bank/12V DC Block 1/3AC1/ON_COIL: RN302.8 (R8.1); also elsewhere on the board
/12V DC Common Bank/12V DC Block 1/3AC1/ON_LED: RN302.9 (R8.2); also elsewhere on the board
/12V DC Common Bank/12V DC Block 1/3AC2/OFF: U301.13 (O6); also elsewhere on the board
/12V DC Common Bank/12V DC Block 1/3AC2/OFF_COIL: RN302.5 (R5.1); also elsewhere on the board
/12V DC Common Bank/12V DC Block 1/3AC2/OFF_LED: RN302.12 (R5.2); also elsewhere on the board
/12V DC Common Bank/12V DC Block 1/3AC2/ON: U301.14 (O5); also elsewhere on the board
/12V DC Common Bank/12V DC Block 1/3AC2/ON_COIL: RN302.6 (R6.1); also elsewhere on the board
/12V DC Common Bank/12V DC Block 1/3AC2/ON_LED: RN302.11 (R6.2); also elsewhere on the board
/12V DC Common Bank/12V DC Block 1/3AC3/OFF: U301.15 (O4); also elsewhere on the board
/12V DC Common Bank/12V DC Block 1/3AC3/OFF_COIL: RN302.3 (R3.1); also elsewhere on the board
/12V DC Common Bank/12V DC Block 1/3AC3/OFF_LED: RN302.14 (R3.2); also elsewhere on the board
/12V DC Common Bank/12V DC Block 1/3AC3/ON: U301.16 (O3); also elsewhere on the board
/12V DC Common Bank/12V DC Block 1/3AC3/ON_COIL: RN302.4 (R4.1); also elsewhere on the board
/12V DC Common Bank/12V DC Block 1/3AC3/ON_LED: RN302.13 (R4.2); also elsewhere on the board
/12V DC Common Bank/12V DC Block 1/3AC4/OFF: U301.17 (O2); also elsewhere on the board
/12V DC Common Bank/12V DC Block 1/3AC4/OFF_COIL: RN302.1 (R1.1); also elsewhere on the board
/12V DC Common Bank/12V DC Block 1/3AC4/OFF_LED: RN302.16 (R1.2); also elsewhere on the board
/12V DC Common Bank/12V DC Block 1/3AC4/ON: U301.18 (O1); also elsewhere on the board
/12V DC Common Bank/12V DC Block 1/3AC4/ON_COIL: RN302.2 (R2.1); also elsewhere on the board
/12V DC Common Bank/12V DC Block 1/3AC4/ON_LED: RN302.15 (R2.2); also elsewhere on the board
/12V DC Common Bank/12V DC Block 1/MultiVibrator3A1/MUX_OFF: U301.2 (I2); also elsewhere on the board
/12V DC Common Bank/12V DC Block 1/MultiVibrator3A1/MUX_ON: U301.1 (I1); also elsewhere on the board
/12V DC Common Bank/12V DC Block 1/MultiVibrator3A1/R1: C301.1, RN303.4 (R3); also elsewhere on the board
/12V DC Common Bank/12V DC Block 1/MultiVibrator3A1/R2: C302.1, RN303.3 (R2); also elsewhere on the board
/12V DC Common Bank/12V DC Block 1/MultiVibrator3A1/RC1: C301.2; also elsewhere on the board
/12V DC Common Bank/12V DC Block 1/MultiVibrator3A1/RC2: C302.2; also elsewhere on the board
/12V DC Common Bank/12V DC Block 1/MultiVibrator3A2/MUX_OFF: U301.4 (I4); also elsewhere on the board
/12V DC Common Bank/12V DC Block 1/MultiVibrator3A2/MUX_ON: U301.3 (I3); also elsewhere on the board
/12V DC Common Bank/12V DC Block 1/MultiVibrator3A2/R1: C303.1, RN303.2 (R1); also elsewhere on the board
/12V DC Common Bank/12V DC Block 1/MultiVibrator3A2/R2: C304.1, RN303.5 (R4); also elsewhere on the board
/12V DC Common Bank/12V DC Block 1/MultiVibrator3A2/RC1: C303.2; also elsewhere on the board
/12V DC Common Bank/12V DC Block 1/MultiVibrator3A2/RC2: C304.2; also elsewhere on the board
/12V DC Common Bank/12V DC Block 1/MultiVibrator3A3/MUX_OFF: U301.6 (I6); also elsewhere on the board
/12V DC Common Bank/12V DC Block 1/MultiVibrator3A3/MUX_ON: U301.5 (I5); also elsewhere on the board
/12V DC Common Bank/12V DC Block 1/MultiVibrator3A3/R1: C305.1, RN303.7 (R6); also elsewhere on the board
/12V DC Common Bank/12V DC Block 1/MultiVibrator3A3/R2: C306.1, RN303.6 (R5); also elsewhere on the board
/12V DC Common Bank/12V DC Block 1/MultiVibrator3A3/RC1: C305.2; also elsewhere on the board
/12V DC Common Bank/12V DC Block 1/MultiVibrator3A3/RC2: C306.2; also elsewhere on the board
/12V DC Common Bank/12V DC Block 1/MultiVibrator3A4/MUX_OFF: U301.8 (I8); also elsewhere on the board
/12V DC Common Bank/12V DC Block 1/MultiVibrator3A4/MUX_ON: U301.7 (I7); also elsewhere on the board
/12V DC Common Bank/12V DC Block 1/MultiVibrator3A4/R1: C307.1, RN303.8 (R7); also elsewhere on the board
/12V DC Common Bank/12V DC Block 1/MultiVibrator3A4/R2: C308.1, RN303.9 (R8); also elsewhere on the board
/12V DC Common Bank/12V DC Block 1/MultiVibrator3A4/RC1: C307.2; also elsewhere on the board
/12V DC Common Bank/12V DC Block 1/MultiVibrator3A4/RC2: C308.2; also elsewhere on the board
/12V DC Common Bank/12V DC Block 2/3AC1/OFF: U1201.11 (O8); also elsewhere on the board
/12V DC Common Bank/12V DC Block 2/3AC1/OFF_COIL: RN1202.7 (R7.1); also elsewhere on the board
/12V DC Common Bank/12V DC Block 2/3AC1/OFF_LED: RN1202.10 (R7.2); also elsewhere on the board
/12V DC Common Bank/12V DC Block 2/3AC1/ON: U1201.12 (O7); also elsewhere on the board
/12V DC Common Bank/12V DC Block 2/3AC1/ON_COIL: RN1202.8 (R8.1); also elsewhere on the board
/12V DC Common Bank/12V DC Block 2/3AC1/ON_LED: RN1202.9 (R8.2); also elsewhere on the board
/12V DC Common Bank/12V DC Block 2/3AC2/OFF: U1201.13 (O6); also elsewhere on the board
/12V DC Common Bank/12V DC Block 2/3AC2/OFF_COIL: RN1202.5 (R5.1); also elsewhere on the board
/12V DC Common Bank/12V DC Block 2/3AC2/OFF_LED: RN1202.12 (R5.2); also elsewhere on the board
/12V DC Common Bank/12V DC Block 2/3AC2/ON: U1201.14 (O5); also elsewhere on the board
/12V DC Common Bank/12V DC Block 2/3AC2/ON_COIL: RN1202.6 (R6.1); also elsewhere on the board
/12V DC Common Bank/12V DC Block 2/3AC2/ON_LED: RN1202.11 (R6.2); also elsewhere on the board
/12V DC Common Bank/12V DC Block 2/3AC3/OFF: U1201.15 (O4); also elsewhere on the board
/12V DC Common Bank/12V DC Block 2/3AC3/OFF_COIL: RN1202.3 (R3.1); also elsewhere on the board
/12V DC Common Bank/12V DC Block 2/3AC3/OFF_LED: RN1202.14 (R3.2); also elsewhere on the board
/12V DC Common Bank/12V DC Block 2/3AC3/ON: U1201.16 (O3); also elsewhere on the board
/12V DC Common Bank/12V DC Block 2/3AC3/ON_COIL: RN1202.4 (R4.1); also elsewhere on the board
/12V DC Common Bank/12V DC Block 2/3AC3/ON_LED: RN1202.13 (R4.2); also elsewhere on the board
/12V DC Common Bank/12V DC Block 2/3AC4/OFF: U1201.17 (O2); also elsewhere on the board
/12V DC Common Bank/12V DC Block 2/3AC4/OFF_COIL: RN1202.1 (R1.1); also elsewhere on the board
/12V DC Common Bank/12V DC Block 2/3AC4/OFF_LED: RN1202.16 (R1.2); also elsewhere on the board
/12V DC Common Bank/12V DC Block 2/3AC4/ON: U1201.18 (O1); also elsewhere on the board
/12V DC Common Bank/12V DC Block 2/3AC4/ON_COIL: RN1202.2 (R2.1); also elsewhere on the board
/12V DC Common Bank/12V DC Block 2/3AC4/ON_LED: RN1202.15 (R2.2); also elsewhere on the board
/12V DC Common Bank/12V DC Block 2/DIG_OFF_C1: RN1201.4 (R3), U1202.4; also elsewhere on the board
/12V DC Common Bank/12V DC Block 2/DIG_OFF_C2: RN1201.9 (R8), U1202.12; also elsewhere on the board
/12V DC Common Bank/12V DC Block 2/DIG_OFF_C3: RN1204.4 (R3), U1203.4; also elsewhere on the board
/12V DC Common Bank/12V DC Block 2/DIG_OFF_C4: RN1204.7 (R6), U1203.12; also elsewhere on the board
/12V DC Common Bank/12V DC Block 2/DIG_ON_C1: RN1201.2 (R1), U1202.1; also elsewhere on the board
/12V DC Common Bank/12V DC Block 2/DIG_ON_C2: RN1201.7 (R6), U1202.9; also elsewhere on the board
/12V DC Common Bank/12V DC Block 2/DIG_ON_C3: RN1204.2 (R1), U1203.1; also elsewhere on the board
/12V DC Common Bank/12V DC Block 2/DIG_ON_C4: RN1204.9 (R8), U1203.9; also elsewhere on the board
/12V DC Common Bank/12V DC Block 2/MultiVibrator3A1/MUX_OFF: U1201.2 (I2); also elsewhere on the board
/12V DC Common Bank/12V DC Block 2/MultiVibrator3A1/MUX_ON: U1201.1 (I1); also elsewhere on the board
/12V DC Common Bank/12V DC Block 2/MultiVibrator3A1/R1: C1201.1, RN1203.4 (R3); also elsewhere on the board
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

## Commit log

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2020-03-14 Most Logic in Place
    [boatcontrol.sch]
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2020-03-16 Fix voltage regulators
    [boatcontrol.sch]
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2020-03-17 Added external RPi connections
    [boatcontrol.kicad_pcb, boatcontrol.sch]
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2020-03-20 Fixed switches
    [boatcontrol.kicad_pcb, boatcontrol.sch]
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2020-03-21 Change do DIP everywhere
    [boatcontrol.kicad_pcb, boatcontrol.sch]
2020-03-22 Time to refactor the PCB
    [boatcontrol.kicad_pcb, boatcontrol.sch]
2020-03-29 Power Routing done on a set
    [boatcontrol.kicad_pcb, boatcontrol.sch]
2020-03-29 Let's sort out the switches
    [boatcontrol.kicad_pcb, boatcontrol.sch]
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2020-03-30 Big Power in place
    [boatcontrol.kicad_pcb, boatcontrol.sch]
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2020-04-04 Split 60A to own daughter board.
    [boatcontrol.kicad_pcb, boatcontrol.sch]
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2020-04-04 Lots of logical cleanup
    [boatcontrol.sch]
2020-04-04 Just need the controller wires now
    [boatcontrol.sch]
2020-04-04 Everything Logically Wired in the Schematic
    [boatcontrol.sch]
2020-04-04 Fix I2C Addresses
    [boatcontrol.kicad_pcb, boatcontrol.sch]
2020-04-05 Add control logic for i2c
    [boatcontrol.kicad_pcb, boatcontrol.sch]
2020-04-05 Going back to restore a multi-pad connector
    [boatcontrol.kicad_pcb, boatcontrol.sch]
2020-04-05 Fixed up High Amp
    [boatcontrol.kicad_pcb, boatcontrol.sch]
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2020-04-06 Address solder jumpers in place
    [boatcontrol.kicad_pcb, boatcontrol.sch]
2020-04-06 Net routing of power and ground
    [boatcontrol.kicad_pcb]
2020-04-07 Let's clean up some power and signals
    [boatcontrol.kicad_pcb, boatcontrol.sch]
2020-04-07 Redesign 12v right
    [boatcontrol.kicad_pcb, boatcontrol.sch]
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2020-04-07 I think it's just clock and signals left
    [boatcontrol.kicad_pcb, boatcontrol.sch]
2020-04-08 More Cleanup, just SCL/SDA left, label cleanup and markings
    [boatcontrol.kicad_pcb]
2020-04-08 Fixed 5v vs. ground to resistor banks, I think wiring is done
    [boatcontrol.kicad_pcb, boatcontrol.sch]
2020-04-08 Fix footprints to use standard DIP
    [boatcontrol.kicad_pcb, boatcontrol.sch]
2020-04-08 Error Free
    [boatcontrol.kicad_pcb]
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2020-04-09 Clean, no stray wires
    [boatcontrol.kicad_pcb]
2020-04-09 Fixed the little mistakes
    [boatcontrol.kicad_pcb]
2020-04-09 Let's Split them up
    [boatcontrol.kicad_pcb]
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2020-04-09 A little more Cleanup
    [boatcontrol.sch]
2020-04-10 Fix vias on daughter board
2020-04-10 Fix RJ45 Power
    [boatcontrol.sch]
2020-04-10 Small fixes
    [boatcontrol.sch]
2020-04-13 Fix RJ45 Connector footprint
    [G5RL_K1A_E.step, SS73100-047F.step, boatcontrol.sch]
2020-04-13 Add 3d and fix capacitors
    [1140-220k-rc.stp, 1140-680k-rc.stp, CUI_DEVICES_TBL008-1000-02BE.step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]
2020-04-13 Fix circuit breakers
    [T9-818.STEP]
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2020-07-08 Refactor into hierarchical sheets
    [boatcontrol.sch]
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2020-07-09 Fix bugs
    [10AmpCircuit.sch, 10_16AmpBlock.sch, 16AmpCircuit.sch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]
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2020-07-09 Fix sheet info
    [10AmpCircuit.sch, 10_16AmpBlock.sch, 16AmpCircuit.sch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]
2020-07-09 Fixed I2C addresses
    [CommonBank1.sch, CommonBank2.sch, MixedControl.sch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]
2020-07-09 Fixed SolderJumpers
    [3AmpBlock.sch, CommonBank1.sch, CommonBank2.sch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]
2020-07-09 Before starting the PCB fresh
    [10AmpCircuit.sch, 10_16AmpBlock.sch, 16AmpCircuit.sch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]
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2020-08-05 Start assigning net classes
    [3AmpBlock.sch, 3AmpCircuit.sch, CommonBank1.sch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]
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2020-08-18 Fix up circuits
    [boatcontrol.kicad_pcb]
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2020-09-10 Restructure power and daughter boards
    [10AmpCircuit.sch, 10_16AmpBlock.sch, 16AmpCircuit.sch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]
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2020-11-18 Move routes to rj45
    [boatcontrol.kicad_pcb, boatcontrol.sch]
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2020-11-18 Fixed daughter board
    [10AmpCircuit.sch, 10_16AmpBlock.sch, 16AmpCircuit.sch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]
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2020-11-19 Before moving resistor bank
    [boatcontrol.kicad_pcb]
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2020-11-19 Lets add some ground to daughter board
    [boatcontrol.kicad_pcb]
2020-11-19 Route missing track
    [CircuitControl.sch, MixedBlock.sch, RelayBoard.sch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]
2020-11-19 Reworked top-signals
    [boatcontrol.kicad_pcb]
2020-11-27 Add multi-vibrator
    [CD74HCT221E.stp]
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2020-11-30 logig to dig name change
    [3AmpBlock.sch, 3AmpCircuit.sch, CommonBank1.sch]
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2020-12-02 Fix extra signals
    [10AmpCircuit.sch, 10_16AmpBlock.sch, 16AmpCircuit.sch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]
2020-12-03 Fix diodes
    [10_16AmpBlock.sch, 3AmpBlock.sch, 6AmpBlock.sch]
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2020-12-15 Fix up 10/16A
    [10AmpCircuit.sch, 10_16AmpBlock.sch, 16AmpCircuit.sch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]
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2020-12-16 Add DC polarity protection
    [3AmpBlock.sch, CommonBank1.sch, CommonBank2.sch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]
2020-12-16 Swich drivers for big relays
    [3AmpBlock.sch, MixedBlock.sch, boatcontrol.sch]
2020-12-16 CRC ErrorFree
    [10AmpCircuit.sch, 10_16AmpBlock.sch, 16AmpCircuit.sch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]
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2020-12-16 Remove resistor on protection, change MOSFET
    [10_16AmpBlock.sch, 3AmpBlock.sch, 3AmpCircuit.sch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]
2020-12-16 Try labels on subcharts
    [10_16AmpBlock.sch, 3AmpCircuit.sch, CommonBank1.sch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]
2020-12-16 Fix graphics
    [10AmpCircuit.sch, 10_16AmpBlock.sch, 16AmpCircuit.sch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]
2020-12-17 Make 12V PSU Optional
    [3AmpBlock.sch, 3AmpCircuit.sch, 6AmpBlock.sch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]
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2020-12-17 Add art and logos
    [boatcontrol.sch]
2020-12-17 Relays and Fuses in place
    [boatcontrol.kicad_pcb, boatcontrol.sch]
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2020-12-17 Fix polarity mosfets
    [3AmpCircuit.sch, CommonBank1.sch, CommonBank2.sch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]
2020-12-17 Add reverse/AC/DC polarity indicators
    [10_16AmpBlock.sch, 3AmpBlock.sch, 3AmpCircuit.sch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]
2020-12-17 Fix AC resistor for polarity indicator
    [CommonBank2.sch]
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2020-12-21 Fix switch logic
    [ESB30B102.step]
2020-12-22 Fix switch layouts
    [10AmpCircuit.sch, 16AmpCircuit.sch, 3AmpBlock.sch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]
2020-12-23 Fix LED resistors
    [10AmpCircuit.sch, 10_16AmpBlock.sch, 16AmpCircuit.sch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]
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2020-12-23 Figure out wiring cluster
    [10AmpCircuit.sch, 10_16AmpBlock.sch, 16AmpCircuit.sch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]
2020-12-24 Add remaining bypass capacitors
    [10AmpCircuit.sch, 10_16AmpBlock.sch, 16AmpCircuit.sch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]
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2020-12-29 Fix second addon board
    [CommonBank2.sch, CommonCathode60A.kicad_pcb, CommonCathode60A.sch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]
2020-12-29 Fix mad hatter
    [3AmpBlock.sch, CircuitControl.sch, CommonBank1.sch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]
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2020-12-29 Big hat fix
    [3AmpBlock.sch, 3AmpCircuit.sch, CircuitControl.sch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]
2020-12-29 RPi scheme update done
    [CommonBank1.sch, CommonBank2.sch, boatcontrol.sch]
2020-12-29 Fixed RPi Footprint
    [3AmpBlock.sch, 3AmpCircuit.sch, CircuitControl.sch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]
2020-12-29 vibrator cleanup and layout
    [boatcontrol.kicad_pcb]
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2020-12-29 Fix addon outlines
    [boatcontrol.kicad_pcb]
2020-12-29 Fix resistor network values
    [3AmpBlock.sch, 6AmpBlock.sch, boatcontrol.kicad_pcb]
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2020-12-30 Fix cap
    [boatcontrol.kicad_pcb]
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2020-12-30 Interal routing for multivibrators done
    [boatcontrol.kicad_pcb]
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2020-12-30 Put solder jumpers in place
    [boatcontrol.kicad_pcb]
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2020-12-31 Fix mosfet
    [3AmpBlock.sch, 3AmpCircuit.sch, CircuitControl.sch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]
2020-12-31 Fix power traces
    [boatcontrol.kicad_pcb]
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2021-01-02 Fix SB footprint and symbol
    [10AmpCircuit.sch, 10_16AmpBlock.sch, 16AmpCircuit.sch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]
2021-01-03 Scale reverse polarity protection
    [CommonBank1.sch, CommonBank2.sch, boatcontrol.kicad_pcb]
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2021-01-04 Add notes about power use of polarity protection
    [3AmpBlock.sch, 3AmpCircuit.sch, CommonBank1.sch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]
2021-01-04 Add warnings and options
    [boatcontrol.sch]
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2021-01-05 Add missing files
    [Sensor.sch]
2021-01-05 Fix power interconnects
    [CurrentSensor.kicad_pcb, CurrentSensor.sch, Sensor.sch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]
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2021-01-05 Add more fets, you can never have enough fets
    [CommonBank1.sch, CommonBank2.sch, boatcontrol.kicad_pcb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]
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2021-01-05 Fix power fills to fets
    [boatcontrol.kicad_pcb]
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2021-01-06 Route vibrators
    [boatcontrol.kicad_pcb]
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2021-01-08 Fix 3d models
    [CUI_DEVICES_TBL008V-1000-02BE.step, boatcontrol.kicad_pcb]
2021-01-08 Fix silkscreen logos and graphics
    [10AmpCircuit.sch, 10_16AmpBlock.sch, 16AmpCircuit.sch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]
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2021-01-11 Time to rewire centre
    [boatcontrol.kicad_pcb]
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2021-01-17 Fix missing symbols
    [boatcontrol.sch]
2021-01-18 Fix rescued symbols
    [10AmpCircuit.sch, 16AmpCircuit.sch, 3AmpCircuit.sch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]
2021-01-22 Fix more rescue stuff
    [boatcontrol.sch]
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2021-02-14 Add xors on input
    [10_16AmpBlock.sch, 3AmpBlock.sch, 6AmpBlock.sch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]
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2021-02-15 Switch to common 5v 10K ohm for an sigs
    [10_16AmpBlock.sch, 16AmpCircuit.sch, 3AmpBlock.sch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]
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2021-02-16 Fix green
    [CommonCathode60A.kicad_pcb, CommonCathode60A.sch, boatcontrol.kicad_pcb]
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2021-02-16 Add text to silkscreen
    [boatcontrol.kicad_pcb]
2021-02-16 Add caps for xors
    [10_16AmpBlock.sch, 3AmpBlock.sch, 6AmpBlock.sch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]
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2021-02-17 I give up, SMD resistors for RJ45
    [10_16AmpBlock.sch, 3AmpBlock.sch, 6AmpBlock.sch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]
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2021-02-27 It kind of fits
    [boatcontrol.kicad_pcb]
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2021-03-01 Fix right
    [10_16AmpBlock.sch, 3AmpBlock.sch, 6AmpBlock.sch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]
2021-03-02 Add Nvidia Jetson stuff
    [boatcontrol.kicad_pcb]
2021-03-03 Hacks and bodges
    [boatcontrol.kicad_pcb]
2021-03-03 Ugly is as ugly does
    [boatcontrol.kicad_pcb]
2021-03-03 Bunch of fracking bullpoop
    [boatcontrol.kicad_pcb]
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2021-03-05 Right side mostly done
    [CircuitControl.sch, boatcontrol.kicad_pcb, boatcontrol.sch]
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2021-03-09 Fix upper routing
    [boatcontrol.kicad_pcb]
2021-03-11 Let's fix this
    [3AmpCircuit.sch, 6AmpBlock.sch, CommonBank1.sch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]
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2021-03-13 again and again and again
    [boatcontrol.kicad_pcb]
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2021-03-18 I guess I removed the heat sink
    [boatcontrol.kicad_pcb]
2021-03-18 Big swap
    [boatcontrol.kicad_pcb]
2021-03-18 Small fix
    [boatcontrol.kicad_pcb]
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2021-03-19 Bugfixes without update
    [boatcontrol.kicad_pcb]
2021-03-19 Rework 6702
    [boatcontrol.kicad_pcb]
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2021-03-22 Before swap
    [3AmpBlock.sch, 6AmpBlock.sch, MultiVibratorA.sch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]
2021-03-22 Good swap
    [boatcontrol.kicad_pcb]
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2021-03-31 work work work, all I do is work :P
    [boatcontrol.kicad_pcb]
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2021-04-01 Fix silly vias
    [boatcontrol.kicad_pcb]
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2021-04-03 Wired
    Only power and I2C left
    (also debugging and fills)
    [boatcontrol.kicad_pcb]
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2021-04-06 Let's fix spacing for power
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2021-04-06 Fix silkscreen
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2021-04-08 Fix 60 Relay board
    [CommonCathode60A.kicad_pcb, CommonCathode60A.sch]
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2021-04-08 Need to trim down 30A addon board traces to 2.7
    [NonLatchingNO30A.kicad_pcb, NonLatchingNO30A.sch]
2021-04-08 Fix readme
    [NonLatchingNO30A.kicad_pcb]
2021-04-08 Fix up silkscreen and numbering
2021-04-09 Final fixes before revision 6
    Fixes to size, dimensions add Revision and hash to board
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2021-04-11 Fix RPi/Jetson footprint
2021-04-11 Fix circuit breaker symbol
    [10AmpCircuit.sch, 16AmpCircuit.sch, 3AmpCircuit.sch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]
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2021-04-16 Fix thermal reliefs for solder pads
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2021-04-26 Fix thermal relief for bottom connector
2021-04-26 Fix some pours and paths
    [3AmpBlock.sch, 3AmpCircuit.sch, MultiVibratorA.sch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]
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2021-05-09 Fix 12v line on bottom for clearance
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
